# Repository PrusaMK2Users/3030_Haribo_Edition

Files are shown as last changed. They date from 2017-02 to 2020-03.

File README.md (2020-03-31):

# 3030 Haribo Edition



[teaser]: http://i.imgur.com/pz1YWP5.jpg "3030 Haribo Edition in Black"

credit: @arobe

## Unaffiliated Statement

We are **not** affiliated with Prusa Research and the work hereafter was done independently / derived from open source files

We are **not** affiliated with any Facebook group, any one claiming the haribo mod / haribo3030 / zaribo mod / etc is doing so on their own and it's not part of the effort

The **ONLY** official source is this github and the **ONLY** official channel to reach us is listed below (mattermost).  

## Contact us

Please join our [Mattermost](http://3dprinting.community) if you want to reach us.

There is a lot of different topics / channels on there, we welcome all with open arms.

## Disclaimer

**you do this modification at your own risk**

we are not responsible for any damages / injuries that might arise from the usage of all material, including but not limited to ideas, documentation, diagrams, that you get from this github.  All precautions and safety protection should be taken and only attempt it if you are experienced in this area.

## Introduction
Inspiration for the project came from [davtr](http://www.thingiverse.com/davtr/about) mk2 conversion [Prusa i3 MK2-X](http://www.thingiverse.com/thing:1692666)

The use of 3030 extrusion makes the frame very rigid and square.  It takes a lot of the guess work out of building the MK2

The name is from the candy that we get when we buy the MK2 kits.  Somebody jokingly said that's a good name and it sort of stuck.

We welcome any contribution to the project, just open a PR (pull request) and we will review and merge changes

## Haribo in the wild

S3D base settings

- 60mm/s 60% other speeds 30% first layer speed
- 80mm/s 50% other speeds 25% first layer speed
- 100mm/s 40% other speeds 20% first layer speed
- 120mm/s 30% other speeds 15% first layer speed

|\#|username|frame/color|Version|60mm/s|80mm/s|>100mm/s|
|-----|-----|-----|-----|-----|-----|-----|
|0|jtktam|Silver/Orange<br/>Silver/Red<br/>Black/Yellow||Yes|Yes|Yes|
|1|geoffreyc|Silver/Orange||Yes|Yes|Yes|
|2|[ar.o.be](http://imgur.com/a/lWbZ5)|Silver/Pineapple||Yes|Yes|Yes|
|3|[joostvwillegen](http://imgur.com/a/RYOfm)|Black/Metallic Gray<br/>Yellow/Carbon||Yes|Yes|Yes|
|4|chinooktx|Silver/Black||Yes|Yes|Yes|
|5|[skuiper](http://imgur.com/a/5j4W8)|Black/Purple+Green||Yes|Yes||
|6|JJ|Black/Violet|||||
|7|satmanager|Silver/Cherry Red||Yes|Yes||
|8|ryanneufeld|Black/Black|||||
|9|tricko|Black/Black+White||Yes|Yes|Yes|
|10|cube||||||
|11|[johnocfii](http://imgur.com/a/TPEzO)|Black/Jade||Yes|||
|12|[jasonh](http://imgur.com/a/vpMrx)|Silver/Transparent||Yes|Yes|Yes|
|13|jonasrh|Black/GITD green|||||
|14|[evad](http://imgur.com/a/PWNlf)|Silver/Silver||Yes|Yes|Yes|
|15|patrik||||||
|16|abjorshammar||||||
|17|stevendpclark||||||
|18|[arb](http://imgur.com/a/QF9FW)|Silver/Lime Green|||||
|19|[philsburry](http://imgur.com/a/lQyBh)|Silver/Translucent Blue|||||
|20|kaiserheld||||||
|21|tcolby|Silver/White|||||
|22|ollietwist|Silver/Orange|||||
|23|Jb3872|Black/Burgundy|||||
|24|unkle_rukus|Black/Neon Green||Yes|Yes|Yes|
|25|carre55|Black/Orange|||||
|26|dark-nico|Silver/Dark Green|||||
|27|olliet|Silver/Patchwork Colors|||||
|28|cova|Black/Translucent Blue|||||
|29|butthurt_beluga|Silver/Orange|||||
|30|jadam|Black/Black|||||
|31|bg|Silver/Patchwork Colors|||||
|32|curt.darius|Silver/Orange|||||
|33|evil4blue|Silver/Blue|||||
|34|nick|?|||||
|35|actibbs|Silver/Translucent Orange|||||
|36|Cappy175|Black/Lime Green|||||
|37|Grooperdude|Black/Dark Pruple|||||
|38|totalitarian||||||
|39|mloidl|Silver/Melon Yellow||Yes|Yes|Yes|
|40|IcicleTrepan|Black/Green|||||
|41|ballzyk0umpa|Black/Orange|||||
|42|[Dino](https://i.imgur.com/nfYLiFp.jpg)|Black/Pink|MK2.5|Yes|Yes|Yes|
|43|skydriver|Silver/Translucent Green||yes|yes|yes|
|44|kstiers|Black/Translucent Sapphire|||||
|45|christherock23|Black/SkyBlue||||
|46|RiskyBirdness|Silver/Red/Black||Yes|Yes|Yes|
|47|SkyDriver|Silver/Green Metallic||N/A|N/A|N/A| 
|48|cdunham1974|Silver/Translucent Magenta||N/A|N/A|N/A| 
|49|psynautic||||||
|50|[devsfan1830](https://imgur.com/gallery/Fj866qR)|Black/Orange|MK2.5||||
|51|[catrielmuller](https://imgur.com/gallery/VBMNfim)|Black/Black|MK2s MMU|Yes|Yes|Yes|

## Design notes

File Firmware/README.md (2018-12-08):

# Firmware

## Releases

Pre-compiled HEX releases can be found here: https://github.com/PrusaMK2Users/Prusa-Firmware/releases

## Introduction

The 3030 Haribo Edition frame has slightly more Z height than the stock Original Prusa i3 MK2. You will need to make some minor modifications to the firmware in order to accommodate for this.

## Warning

**Please Note:** Depending on the y carriage you use (stock or aftermarket), your mileage might vary.  Various y-carriages have different heights. I will note where you need to make the necessary changes and how to determine the values, but be ready to shut down the machine if it looks like it's going to crash the head into the bed!

## Configuration_prusa.h

Let's change the name of the printer:

```
// Printer name
#define CUSTOM_MENDEL_NAME "3030 Haribo Edition"
```

Let's set the correct Z_MAX_POS, the originial value is 210, and after a few test builds we determine 220 works on the MK2 and MK2s

so let's set it to 220:

```
#define Z_MAX_POS 220
```

If using the MK2.5 you'll need to change the Z_MAX_POS to 225mm due to the new MK52 bed

so let's set it to 225:

```
#define Z_MAX_POS 225
```

## Configuration.h

Since we are in here anyways, let's fix the encoder too:

```
#define ENCODER_PULSES_PER_STEP 2 // Increase if you have a high resolution encoder
#define ENCODER_STEPS_PER_MENU_ITEM 2 // Set according to ENCODER_PULSES_PER_STEP or your liking
```

to

```
#define ENCODER_PULSES_PER_STEP 4 // Increase if you have a high resolution encoder
#define ENCODER_STEPS_PER_MENU_ITEM 1 // Set according to ENCODER_PULSES_PER_STEP or your liking
```

## pins.h (optional)

Now depending which LCD board you have, you might find the rotary wheel direction is not intuitive (goes up when you expect down, down when up).  It's fairly easy to fix.  You need to invert 2 numbers in pins.h  

Find the first occurence of the following lines:
```
#define BTN_EN1 72
#define BTN_EN2 14
```

These are the atmega pin numbers assigned to the up and down motion of the menus.  To invert them, simply swap the numbers so the lines become:
```
#define BTN_EN1 14
#define BTN_EN2 72
```

## Final step

Now compile and upload the firmware.. redo your xyz calibration as normal

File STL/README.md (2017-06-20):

# STL

## Quantity to print
Beginning of each filename denotes the quantity of that part you need to print.

for example

1x_power_supply_box.stl means you should print one.

## Stock MK2 parts

Any parts not found in this github you can find on [prusa research github](https://github.com/prusa3d/Original-Prusa-i3/tree/MK2)

## Print settings

All models should be printed as oriented in the STL files

No supports are needed

30% infill, triangular or fast honeycomb for strength
3/3/2 top/bottom/perimeters
0.2mm layer height
PETG is preferred

ABS might have shrinkage issues on some parts
PLA is not preferred, will eventually need replacements due to fatigue

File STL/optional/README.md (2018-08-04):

# Optional STL

_These files are optional stuff to print for the Haribo Edition_

|Filename|Author|Description|
|-----|-----|-----|
|1x 67.75mm Jig.stl|jtktam|A jig to set the spacing of the left y rod holders to 67.75mm.  don't worry if it's not dead on, the idea is using this will ensure the front and back *LEFT* side y rod holders are the same distance from the left edge of the extrusion.  the holes are for M6 x 12 bolts and t-nuts, it's *suppose* to be loose so you can slide it in and out quickly.  Tested and it works to ensure the left side is good to go|
|1x_aftermarket_y_carriage_raiser.stl|jtktam (Joseph Tam)|three sc8uu block spacers and 1 belt holder spacer to raise the y carriage by 3.5mm to match the level of the stock y carriage|
|1x_fan-nozzle-haribo.scad<br/>1x_fan-nozzle-haribo.stl|jonasrh (Jonas Hansen)|a special version of the fan nozzle with "Haribo" on it|
|1x_lcd_cover.stl<br/>1x_lcd_cover.scad<br/>BPreplayBold.otf|Cova (Rob Baumstark)|Updated version of the LCD cover with '3030 Haribo Edition'. SCAD source included to generate custom LCD covers with your number in the corner and optionally updated text for dual-color.<br/>Included BPreplay font required to compile the SCAD source.|
|1x_lcd_cover_text.stl|Cova (Rob Baumstark)|STL of the text in the LCD cover for dual-color prints.|
|1x_lcd_mount_3030_clips.stl|nrepian|Modified LCD mount to use clips, rather than insert|
|1x_lcd_mount_3030_extra_contrast_clearance.stl|nrepian|3030 LCD clips with additional clearance for contrast pot|
|1x_lcd_mount_extra_contrast_clearance.stl|stevendpclark (Steven Clark)|A version of the LCD mounts that provide more clearance for the contrast pot for 3rd Party 2004 LCD Smart Controller Display boards.|
|1x_mk2x_y_belt_holder.stl|Mk2-x|demoted y belt holder|
|1x_mk2x_y_belt_holder_modded.stl|chinooktx (Pat Brochu)|modded y belt holder from mk2x (added 2mm)|
|1x_power_supply_box.stl<br/>1x_power_supply_mount.stl|jtktam (Joseph Tam)|Power supply mount and switch box for ebay PSU|
|1x_rambo_mount.stl|ryanneufeld (Ryan Neufeld)|Adapter plate to allow using the Prusa rambo enclosure.|
|1x_z_motor_mounts_three_screw.stl|dino (Garrett B)|Removed front inner screw holes to prevent collisions with pinda/fan nozzle|
|3x_double_y_bearing_housing.stl|Mk2-x|demoted y bearing holder|
|3x_SC8UU_LM8UU.stl|jtktam (Joseph Tam)|adapt lm8u to sc8uu block, use for aftermarket y carriage|
|3x_SC8UU_RZJM.stl|jtktam (Joseph Tam)|adapt igus rjzm to sc8uu block, use for aftermarket y carriage|
|3x_y_bearing_housing_lm8uu_short.stl|chinooktx (Pat Brochu)|adapt lm8uu to y belt bearing|
|3x_y_bearing_housing_rjzm_01_08.stl|chinooktx (Pat Brochu)|adapt igus rjzm to y belt bearing|
|7x_tsun_end_cap.stl|Cova (Rob Baumstark)|End caps designed to fit T-Sun 3030 extrusion|
|16mm Tnut Spacing|davvyk/dino (Garrett B)|Widened spacing between blocks to accomodate 15.8mm Tnuts|
|i3 Haribo Rambo Mount Thin.stl|ARBBB|Use for mounting standard rambo enclosure to the Haribo extrusions.|
|LED_Holder_Haribo_v3.stl | John O'Shaughnessy (johnocfii) and Patrik Rosén (patrik) | LED Strip/Bar Holders that attach to the back side of the Haribo frame.  Use this if you didn't use plastic L brackets on the top of the Z frame or if you did use plastic L brackets but only need a narrow area to hold your LEDs as the L brackets will prevent you from using the full back side of the extrusion.|
|LED_Holder_Haribo_v3_Bracket_Mount.stl | IcicleTrepan | Yet another alternate version of the excellent LED Strip/Bar Holder by John/Patrik.  This one can attach to the back side of the extrusion over top of the L brackets, giving you use of most of the back side of the Z frame's extrusion (still have to watch out for the hex screws).  NOTE:  It may be easier to install beside the bracket and then slide over the bracket than to install directly on the bracket.|
|LED_Holder_Haribo_v3_Reversed_Mount.stl | IcicleTrepan | Alternate version of the excellent LED Strip/Bar Holder by John/Patrik.  This one attaches to the front side of the Haribo frame.  Use this if you did use plastic L brackets on the Z frame and would like the holders spread out further.|
|LRS-350-12-bottom.stl|chinooktx (Pat Brochu)|Initial design for LRS-350-12 Meanwell Power Supply bottom cover|
|LRS-350-12-top.stl|chinooktx (Pat Brochu)|Initial design for LRS-350-12 Meanwell Power Supply top bracket|
|LRS-350-Neuf/LRS-350 Enclosure (lid and body) | Ryan Neufeld | Enclosure designed for IEC with integrated switch, and a removable lid for ease of access. Use M3x8mm fasteners w/ M3 nuts. Optionally you can use M3x10 or longer if you don't want to use nuts the hole beyond the nut is sized for direct threading of M3 fasteners.| 
|MK2S-modified-y-belt-holder.stl| Ryan Neufeld | A wider version of the stock mk2s belt holder, allows for re-positioning to better align with the PINDA when homing.|
|MK2S-modified-y-belt-holder-3mm-taller.stl| Ryan Neufeld | As above, only pushes the belt down 3mm, this is to be used in leiu of the belt holder spacer when using the half height bed frame.|
|Spool-holder-slide-top.stl|MoshiBin | A spool holder that sits on top of the frame, slides from the side of the top extrusion. Modeled to be similar to the "B4" MK3 spool mount.|

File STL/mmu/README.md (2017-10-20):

# Multi-Material Upgrade Parts

|Filename|Author|Description|
|-----|-----|-----|
|1x_e_motor_holder.stl| Ryan Neufeld (ryanneufeld)  | Remixed mounts for the mmu extruders. You need one per pair of colors. 2 colors == one part, 4 colors == two parts | 
|1x_superswitch_adapter.stl | Ryan Neufeld (ryanneufeld) | An adapter plate that will allow you to use the Prusa superswitch enclosure on the haribo. |
|1x_superswitch_mount.stl | RydinX (Jonas Hansen) | A superswitch mount inspired by the rambo mount designed by Joseph Tam|

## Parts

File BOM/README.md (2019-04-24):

# I. Introduction
Below you will find the Bill of Materials for the **3030 Haribo Edition** build. This BOM will help you to either **upgrade** your **Original Prusa i3 MK2** or **scratch-build** a printer. Each section contains a subheading to indicate if it's required for an **upgrade** or just a **scratch-build**. If you have questions about this build, feel free to submit a Github issue and we will be glad to help you.

# II. Aluminum Frame Parts / Smooth Rods / Rubber Feet
#### Required For: **Upgrade** / **Scratch-Build**
This section contains the frame parts, smooth rods, t-slot nuts, and rubber feet that you will need.

If you live in the United States, the recommended seller of these parts is [Misumi US](https://us.misumi-ec.com/). To simplify the ordering process from Misumi, we have created a [Misumi CSV guide here](./MISUMI_CSV/README.md). You can simply download a pre-made data file and upload it to your cart to order all of the required parts.

If you would rather source the frame parts elsewhere, below is a list of all of the frame parts you will need.

#### Parts List

|Qty|Misumi Part #|Description|
|-----|-----|-----|
|3|HFS6-3030-354-Z8-XA12-XB342|Clear anodize 3030 Normal Rigidity Type extrusion 354mm 8mm counterbore hole @ 12mm and 342mm (x)|
|2|HFS6-3030-320-TPW-Z8-XA100|Clear anodize 3030 Normal Rigidity Type extrusion 320mm tap both ends 8mm counterbore hole @100mm (y)|
|2|HFS6-3030-330-TPW|Clear anodize 3030 Normal Rigidity Type 330mm tap both ends (z)|
|2|PSFG8-370|Hard Chrome Precision Linear Shaft - Straight 370mm (x)|
|2|PSFG8-360|Hard Chrome Precision Linear Shaft - Straight 360mm (y)|
|2|PSFG8-320|Hard Chrome Precision Linear Shaft - Straight 320mm (z)|
|1|PACK-HNTTSN6-6|Pre-Assembly Insertion Short Nuts -For HFS6 Series Aluminum Extrusions (100 per pack)|
|4|C-30-RK-3617|Rubber Feet|

#### Misc Misumi Parts (Scratch build only)

|Qty|Misumi Part #|Description|
|-----|-----|-----|
|2|WM5-15|Extruder Springs (5x15mm)|
|1|PSFR5-16|Extruder idler bearing rod(5x16mm)|

#### Spool Holder Parts List (OPTIONAL)
If you would like to build an integrated spool holder, there are a few other parts you will need.

|Qty|Misumi Part #|Description|
|-----|-----|-----|
|1|HFS6-3030-200-Z8-XA15|Clear anodize 3030 High Rigidity Type extrusion 200mm 8mm counterbore hole @ 15mm (spool holder vertical)|
|1|HFS6-3030-147-LTP|Clear anodize 3030 High Rigidity Type extrusion 147mm tap left end (spool holder horizontal)|
|1|SHBLBSL6|Brackets - 6 Series, Blind Brackets |

# III. Mounting Hardware
#### Required For: **Upgrade** / **Scratch-Build**

You will need some various nuts and bolts in order to assemble your **3030 Haribo Edition**. Below you will find a list of required hardware for both an upgrade build and a scratch printer build.

#### Recommended sources for this section (United States)
- [Bolt Depot](http://www.boltdepot.com/)
- [McMaster-Carr](https://www.mcmaster.com)
- [Fastenal](https://www.fastenal.com/)

#### Parts List
|Qty|Description|
|-----|-----|
|36|M6 washer|
|9|Socket Head Cap Screw M8 x 40mm|
|12|Socket Head Cap Screw M6 x 12mm|
|54|Socket Head Cap Screw M6 x 14mm|
|4|Socket Head Cap Screw M6 x 20mm|

# IV. Bushings
If you are upgrading from an Original Prusa i3 MK2, you may re-use the **LM8UU** bushings for X, Y and Z axes. However, you may consider swapping the X and Y axes with IGUS Drylin® Bushings. **Caution**: It is NOT recommended to use these bushings on the Z axis, as it is prone to binding on the **3030 Haribo Edition**.

#### Parts List
|Qty|Part #|Description|
|-----|-----|-----|
|6|RJ4JP-01-08|IGUS DRYLIN® Bushing|

#### Recommended sources for this section (United States)
- [Folger Technologies](https://goo.gl/oc9qrd)

# V. Scratch Build Parts
#### Required For: **Scratch-Build**
This section is only required for users who are building a **3030 Haribo Edition** from scratch.

#### Parts List

|Qty|Part #|Source|Description|
|-----|-----|-----|-----|
|1|PRI-UPG-MK2-ORG|[Prusa Research](https://goo.gl/39exUd)|Original Prusa i3 Plus to MK2 upgrade kit |
|1|-|[ultimachine](https://goo.gl/L4XLX0)|Rambo Mini v1.3 |
|1|LRS-350-12|[Arrow](https://goo.gl/zRQ6IZ) |Meanwell LRS-350-12 12V 29A 348W Power Supply |
|1|-|eBay / aliexpress|IEC power socket |
|1|-|eBay / aliexpress|Power switch |
|1|E-FAN-50-50-15|[e3D](https://goo.gl/qESKpZ)|50x50x15mm 12v DC Side Blow Fan |
|1|-|[RepRap Champion](https://goo.gl/xK2OkY) / eBay / aliexpress| Smart controller Reprap 2004 LCD |
|2|-|eBay / aliexpress|2x5 ribbon cable (>40cm) |
|-|-|Electronics Store|14awg power wire (black/red) |
|-|-|Electronics store|14awg ferrules |
|-|-|Electronics Store|Short zip ties (just get a bag full) |
|1|-|Electronics Store / Amazon | Wire loom (3/8" or 10mm) (For wire management)|
|1|-|[RepRap Champion](https://goo.gl/54I3IC) / eBay / aliexpress|Prusa i3 Universal Y Carriage Plate|
|2|-|[RepRap Champion](https://goo.gl/VUj4mo) / eBay / aliexpress|GT2 16T pulley|
|4|F623ZZ|eBay / aliexpress|F623ZZ 3x10x4mm flanged bearing. Put two of them together so the flange size faces out as belt idler. |
|1|104138|eBay / Hobby Store|HPI Blitz / Firestorm Titanium Idler Gear Shaft 5x16m #104138 (For extruder idler bearing rod)|
|4|-|[RepRap Champion](https://goo.gl/8F2Ub6) / eBay / aliexpress|LM8UU linear bearing (Bearings for the X Ends (Z Movement Direction) |
|8|-|McMaster / Fastenal / Bolt Depot | M3 fender washer |
|2|-|McMaster / Fastenal / Bolt Depot | M5 fender washer |
|4|-|McMaster / Fastenal / Bolt Depot | M2 washer |
|14|-|McMaster / Fastenal / Bolt Depot | M3 washer |
|6|-|McMaster / Fastenal / Bolt Depot | M3 square nut |
|2|-|McMaster / Fastenal / Bolt Depot | M3 lock nut|
|9|-|McMaster / Fastenal / Bolt Depot | M3 hex nut|
|4|-|McMaster / Fastenal / Bolt Depot | Socket Head Cap Screw M2 x 12mm|
|15|-|McMaster / Fastenal / Bolt Depot | Socket Head Cap Screw M3 x 10mm|
|6|-|McMaster / Fastenal / Bolt Depot | Socket Head Cap Screw M3 x 12mm|
|10|-|McMaster / Fastenal / Bolt Depot | Socket Head Cap Screw M3 x 18mm|
|3|-|McMaster / Fastenal / Bolt Depot |Socket Head Cap Screw M3 x 20mm|
|2|-|McMaster / Fastenal / Bolt Depot |Socket Head Cap Screw M3 x 25mm|
|3|-|McMaster / Fastenal / Bolt Depot |Socket Head Cap Screw M3 x 30mm|
|3|-|McMaster / Fastenal / Bolt Depot |Socket Head Cap Screw M3 x 40mm|
|5|-|McMaster / Fastenal / Bolt Depot |Button Head Cap Screw M3 x 8mm|
|4|-|McMaster / Fastenal / Bolt Depot |Button Head Cap Screw M3 x 10mm|
|2|-|McMaster / Fastenal / Bolt Depot |Button Head Cap Screw M3 x 12mm|
|4|-|McMaster / Fastenal / Bolt Depot |Button Head Cap Screw M4 x 6mm|
|9|-|McMaster / Fastenal / Bolt Depot |Socket Head Cap Screw M8 x 40mm|
|12|-|McMaster / Fastenal / Bolt Depot |Socket Head Cap Screw M6 x 12mm|
|54|-|McMaster / Fastenal / Bolt Depot |Socket Head Cap Screw M6 x 14mm|
|4|-|McMaster / Fastenal / Bolt Depot |Socket Head Cap Screw M6 x 20mm|

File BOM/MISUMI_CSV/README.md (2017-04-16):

# Introduction
Regardless of whether you are upgrading from an existing Original Prusa i3 MK2,
or building a 3030 Haribo Edition from scratch, you will need to order aluminum
extrusions, smooth rods, t-slot nuts. Our current recommended source for these
parts (for those living in the US) is from [Misumi USA](https://www.misumi-ec.com/us).

To make the Misumi ordering process simpler, we have put together a CSV (Comma-separated Value) file containing all of the parts for the 3030 Haribo Edition. This file can be uploaded to your Misumi cart using the instructinos below.

# 1. Pick your color!
Decide whether you would like a silver frame or a black frame. Choose a color and then download the appropriate corresponding CSV file below based on your selection.

- [Silver 3030 Frame CSV File](./Misumi_Haribo_Upgrade_Parts_Silver.csv)
- [Black 3030 Frame CSV File](./Misumi_Haribo_Upgrade_Parts_Black.csv)

# 2. Do you also want an integrated spool holder?
If you would like to also build a spool holder, you can also download a CSV file containing those additional parts below:

- [Silver](./Misumi_Haribo_SpoolHolder_Silver.csv)
- [Black](./Misumi_Haribo_SpoolHolder_Black.csv)

# 3. Order the parts!

- **Step 1.** Register an account with Misumi [here](https://us.misumi-ec.com/contents/regist/)
- **Step 2.** Login to your Misumi account.
- **Step 3.** Select the "Order" link at the top of the page.

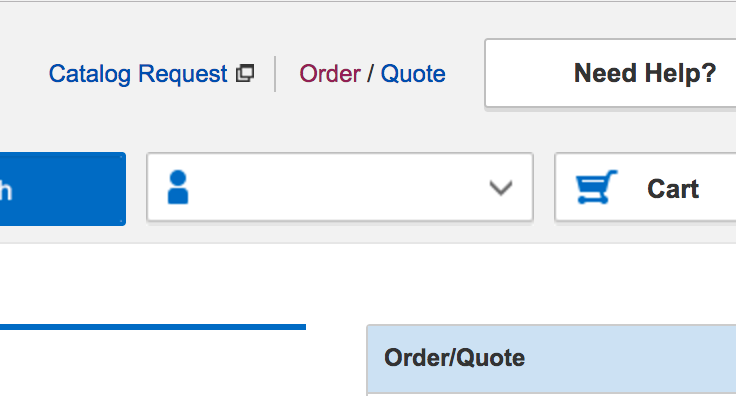
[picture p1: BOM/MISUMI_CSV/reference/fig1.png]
Order Link


- **Step 4.** Scroll down to the bottom of the "Create Order Request" page and click "Import from File".

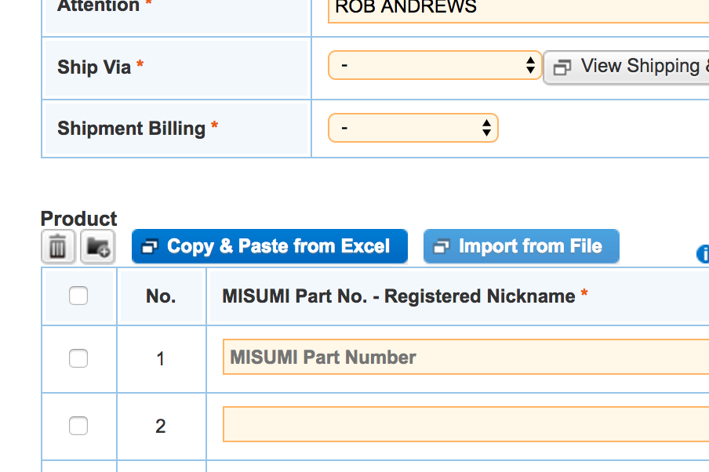
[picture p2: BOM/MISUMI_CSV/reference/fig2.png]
Import From File


- **Step 5**. On the "Import From File", select "Choose File" and select the CSV for the main Haribo parts that you previously downloaded. This file should begin in "Misumi_Haribo_Upgrade_Parts_". If you also downloaded the spool holder CSV, repeat this process once you have finished importing the first CSV file by returning to Step 4.

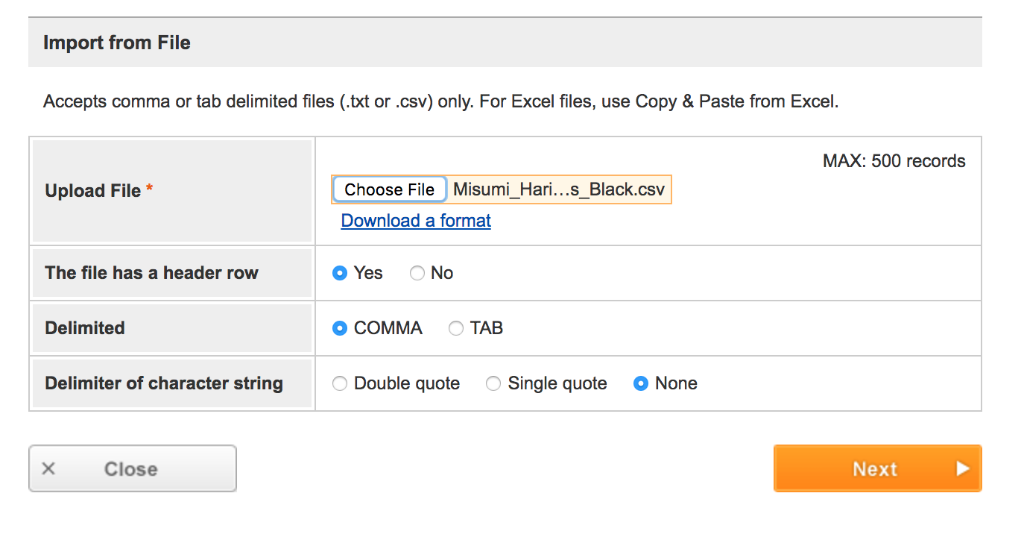
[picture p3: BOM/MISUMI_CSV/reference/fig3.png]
Import CSV


- **Step 6.** On the "Import From File" screen, verify you select the following options:
  - **This file has a header row**: `Yes`
  - **Delimited**: `COMMA`
  - **Delimiter of character string**: `None`
- **Step 7.** Click 'Next' on the "Import from File" screen.
- **Step 8.** Click 'Next' on the "Set Item" screen.

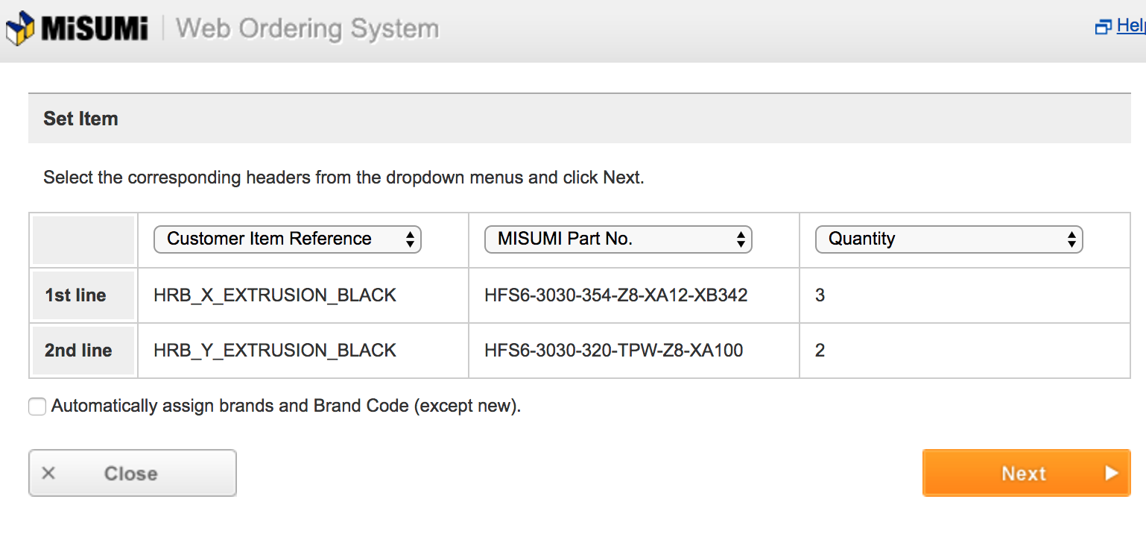
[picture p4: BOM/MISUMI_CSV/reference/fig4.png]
Set Item Screen


- **Step 9.** The items should now be in your cart.
- **Step 10.** If you would like to upload the CSV for the Optional Spool Holder, continue back to **Step 4**. Otherwise, continue to **Step 11**.
- **Step 11.** Continue to fill out the remainder of the Order Form and submit your Misumi order. Congrats on ordering your Haribo parts!

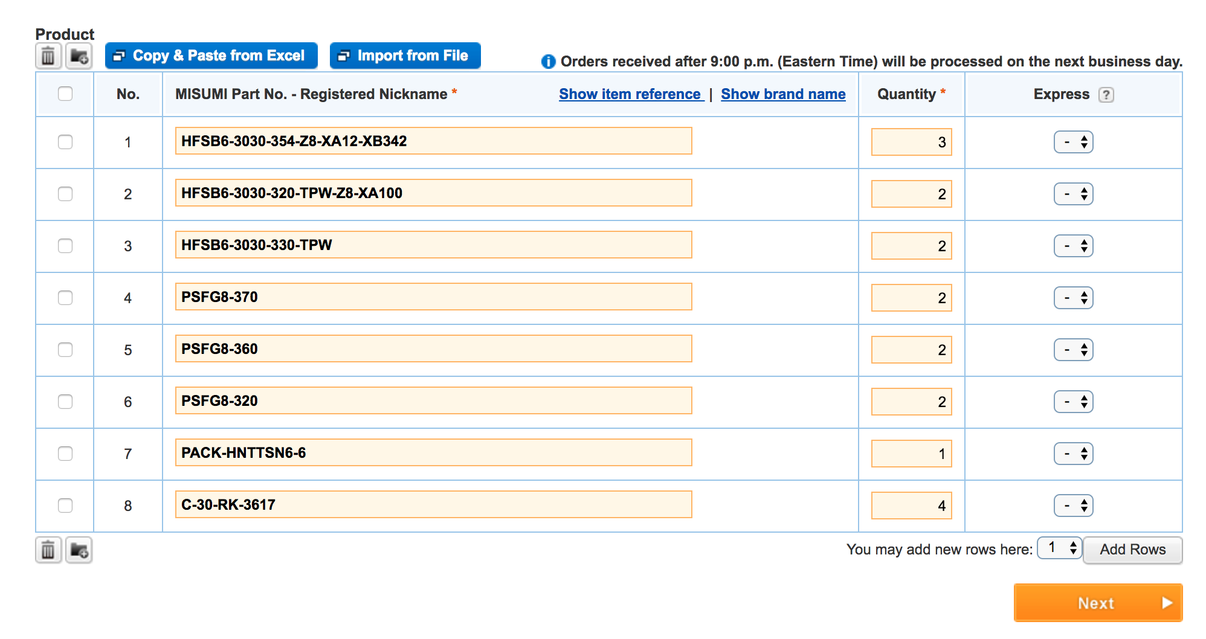
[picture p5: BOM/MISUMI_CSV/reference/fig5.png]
Items Added to Cart


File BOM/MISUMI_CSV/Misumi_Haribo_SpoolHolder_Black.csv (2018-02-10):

Customer Item Reference | MISUMI Part No. - Registered Nickname | Quantity
HRB_SPOOLHOLDER_HORZ_BLACK | HFSB6-3030-200-Z8-XA15 | 1
HRB_SPOOLHOLDER_VERT_BLACK | HFSB6-3030-147-LTP | 1
HRB_MOUNTING_BRACKET | SHBLBSL6 | 1

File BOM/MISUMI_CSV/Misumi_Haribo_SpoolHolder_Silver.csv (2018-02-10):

Customer Item Reference | MISUMI Part No. - Registered Nickname | Quantity
HRB_SPOOLHOLDER_HORZ_SILVER | HFS6-3030-200-Z8-XA15 | 1
HRB_SPOOLHOLDER_VERT_SILVER | HFS6-3030-147-LTP | 1
HRB_MOUNTING_BRACKET | SHBLBSL6 | 1

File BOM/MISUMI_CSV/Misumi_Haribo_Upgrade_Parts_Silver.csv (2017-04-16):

Customer Item Reference | MISUMI Part No. - Registered Nickname | Quantity
HRB_X_EXTRUSION_SILVER | HFS6-3030-354-Z8-XA12-XB342 | 3
HRB_Y_EXTRUSION_SILVER | HFS6-3030-320-TPW-Z8-XA100 | 2
HRB_Z_EXTRUSION_SILVER | HFS6-3030-330-TPW | 2
HRB_X_SMOOTH_ROD | PSFG8-370 | 2
HRB_Y_SMOOTH_ROD | PSFG8-360 | 2
HRB_Z_SMOOTH_ROD | PSFG8-320 | 2
HRB_T_SLOT_NUTS | PACK-HNTTSN6-6 | 1
HRB_RUBBER_FEET | C-30-RK-3617 | 4

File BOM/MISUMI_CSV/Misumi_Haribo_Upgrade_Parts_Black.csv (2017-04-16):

Customer Item Reference | MISUMI Part No. - Registered Nickname | Quantity
HRB_X_EXTRUSION_BLACK | HFSB6-3030-354-Z8-XA12-XB342 | 3
HRB_Y_EXTRUSION_BLACK | HFSB6-3030-320-TPW-Z8-XA100 | 2
HRB_Z_EXTRUSION_BLACK | HFSB6-3030-330-TPW | 2
HRB_X_SMOOTH_ROD | PSFG8-370 | 2
HRB_Y_SMOOTH_ROD | PSFG8-360 | 2
HRB_Z_SMOOTH_ROD | PSFG8-320 | 2
HRB_T_SLOT_NUTS | PACK-HNTTSN6-6 | 1
HRB_RUBBER_FEET | C-30-RK-3617 | 4

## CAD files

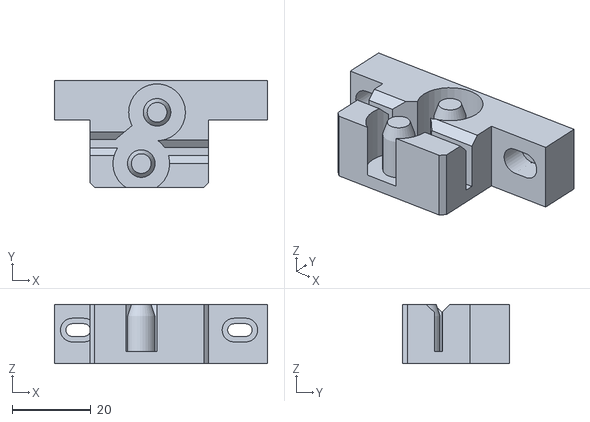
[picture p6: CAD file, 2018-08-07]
STL/1x_y_belt_holder.stl
54.0 x 27.0 x 15.0

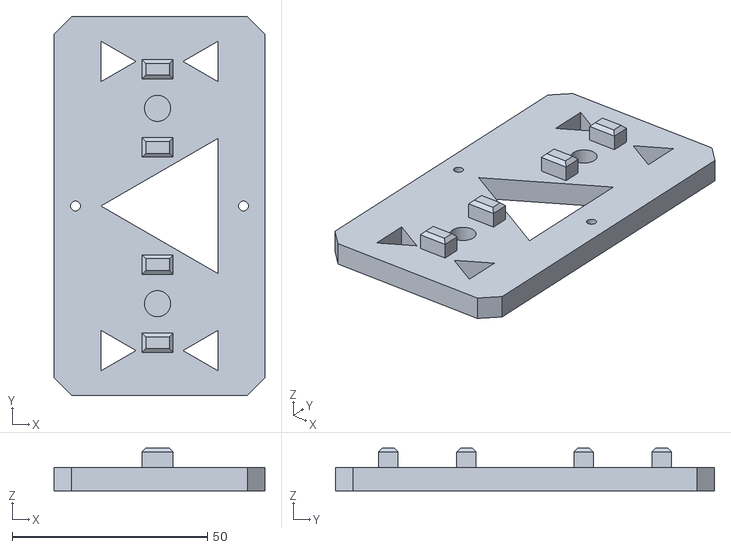
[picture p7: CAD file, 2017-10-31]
STL/mmu/1x_superswitch_v2_mount.stl
54.0 x 97.0 x 11.0

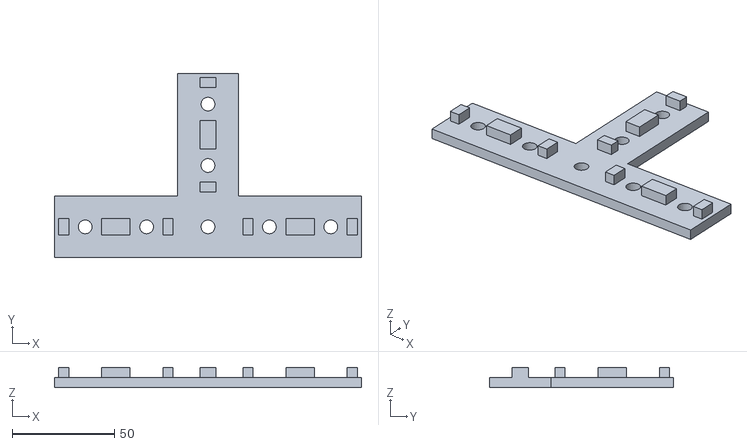
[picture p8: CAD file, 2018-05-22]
STL/optional/16mm Tnut Spacing/2x_T_bracket_16mm.stl
150.0 x 90.0 x 10.0

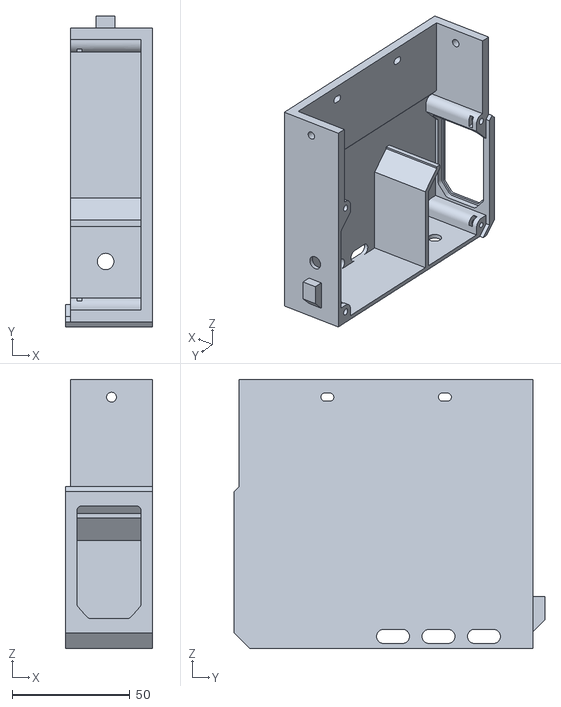
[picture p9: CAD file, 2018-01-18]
STL/optional/LRS-350-Neuf/1x_LRS-350_enclosure_body.stl
37.1 x 132.1 x 114.4

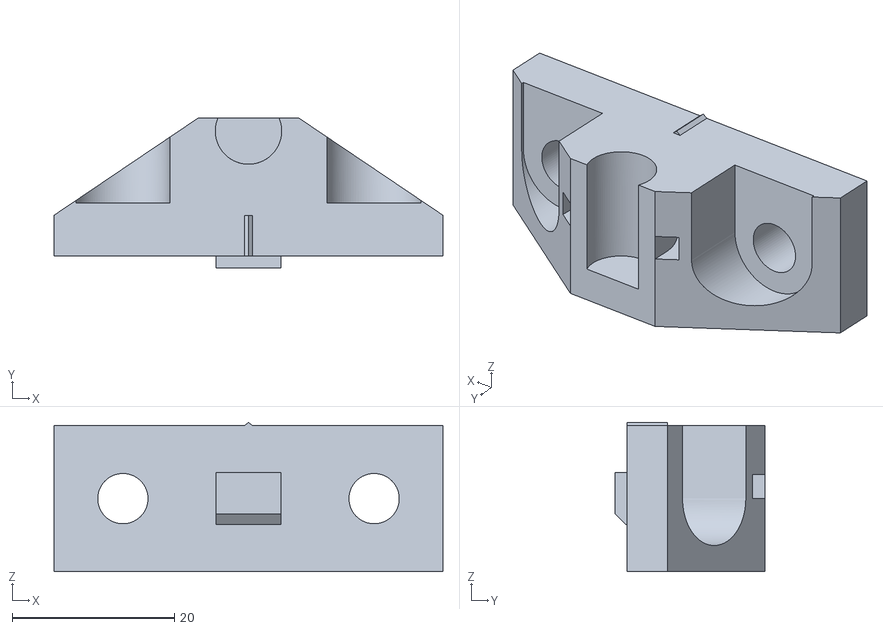
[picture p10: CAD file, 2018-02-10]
STL/square_slot_extrusions/4x_y_rod_holder_SSE.stl
48.0 x 18.5 x 18.4

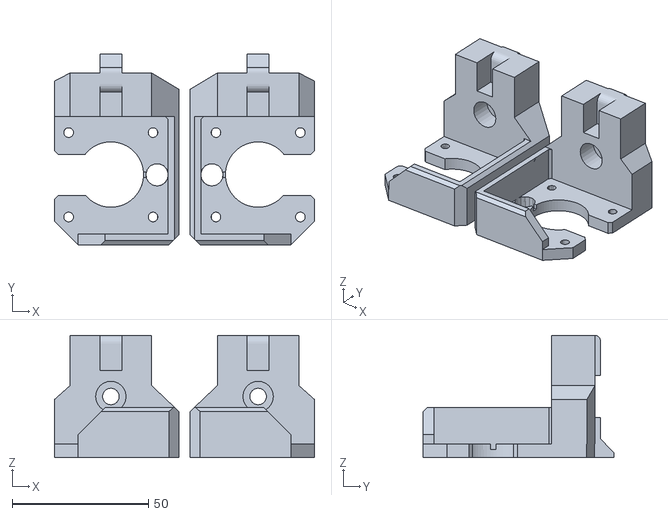
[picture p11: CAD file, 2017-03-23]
STL/1x_z_motor_mounts.stl
95.5 x 70.0 x 45.0

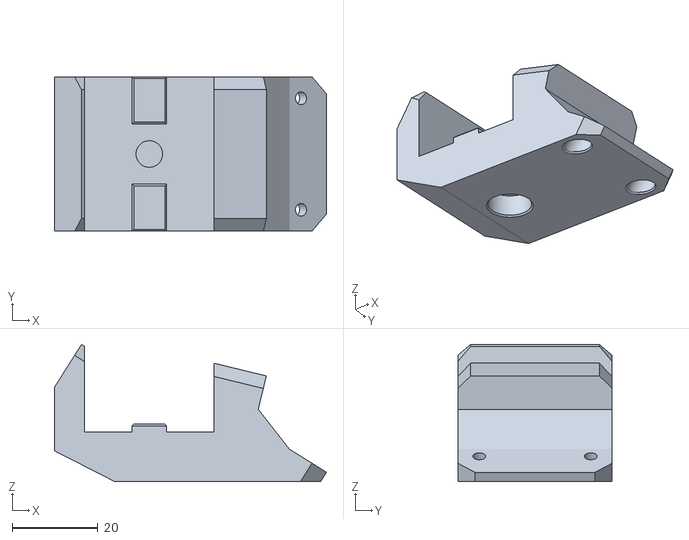
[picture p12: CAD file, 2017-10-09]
STL/mmu/1x_e_motor_holder.stl
63.4 x 36.0 x 31.9

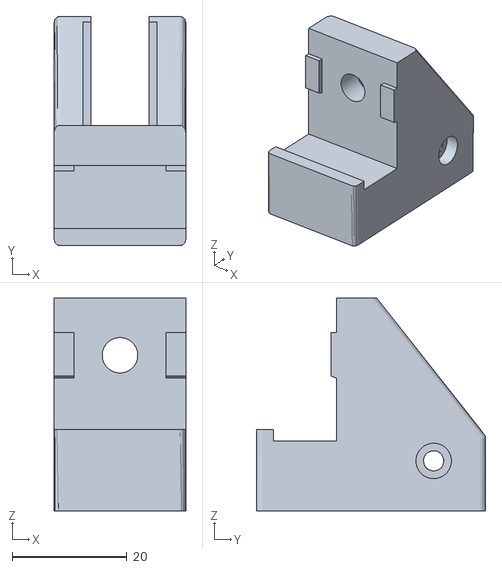
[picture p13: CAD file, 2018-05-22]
STL/optional/16mm Tnut Spacing/1x_y_idler_16mm.stl
23.0 x 40.0 x 37.2

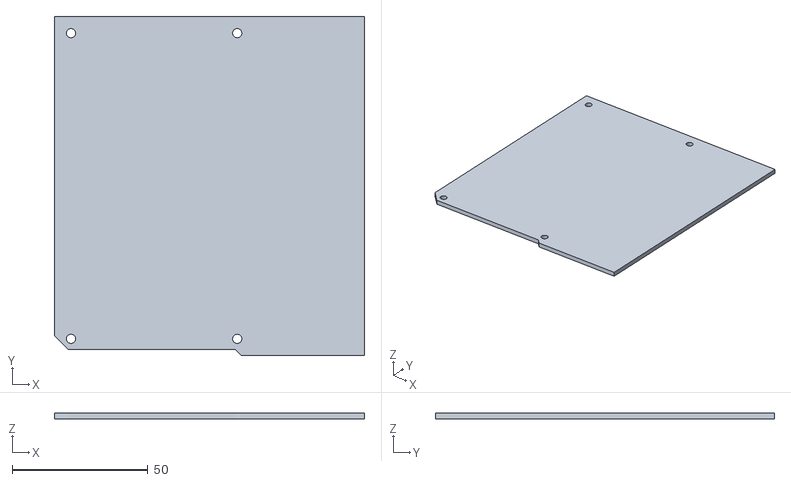
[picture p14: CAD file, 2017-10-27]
STL/optional/LRS-350-Neuf/1x_LRS-350_enclosure_lid.stl
114.4 x 125.0 x 2.15

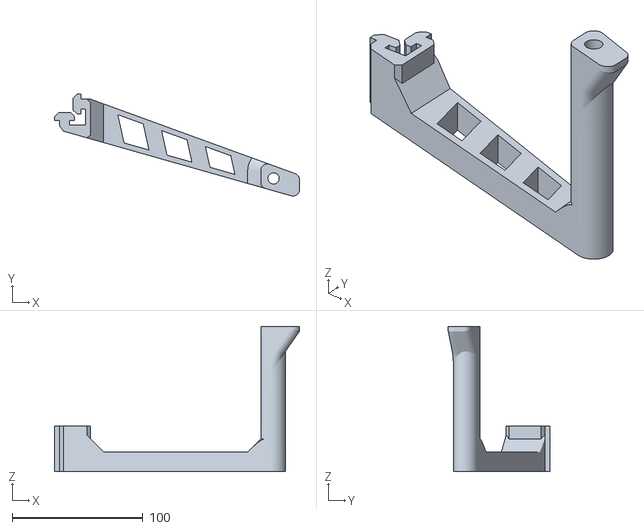
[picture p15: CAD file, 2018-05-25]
STL/optional/Spool-holder-slide-top.stl
187.4 x 78.1 x 111.0

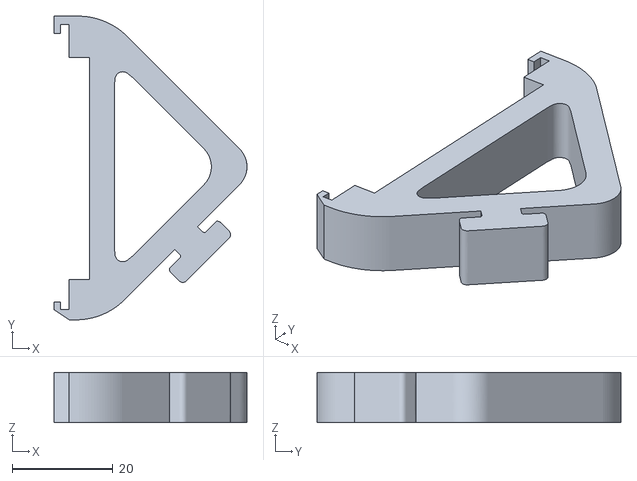
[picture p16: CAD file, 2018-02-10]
STL/square_slot_extrusions/1x_lcd_mount_extended_pcb_ears_part1_SSE.stl
38.3 x 60.2 x 10.0

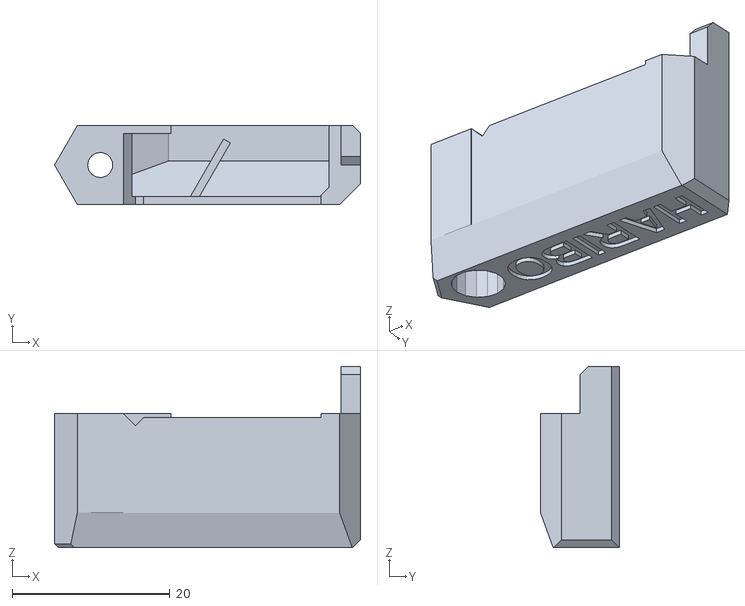
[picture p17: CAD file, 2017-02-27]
STL/1x_fan-nozzle-haribo.stl
38.8 x 10.0 x 23.0

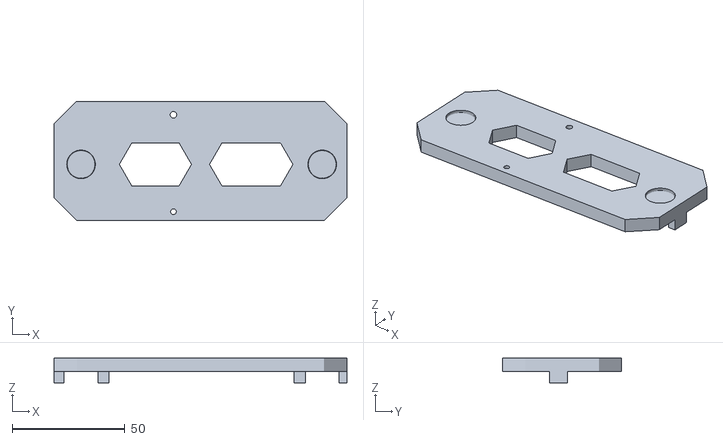
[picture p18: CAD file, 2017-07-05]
STL/mmu/1x_superswitch_adapter.stl
130.0 x 53.0 x 11.0

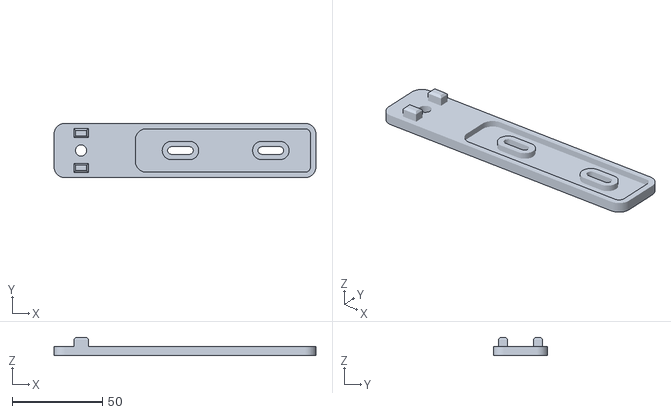
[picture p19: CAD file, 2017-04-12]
STL/optional/LRS-350-Neuf/1x_LRS-350_psu_upper_strap.stl
145.0 x 30.0 x 10.0

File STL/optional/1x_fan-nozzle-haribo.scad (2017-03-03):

module fan_nozzle(){
    difference(){    
        union(){
            cube([32,10,17]); // Main cube
            translate([30,5,0])cylinder(r=5.8,h = 17, $fn=6);    
            translate([-3,0,-6]) cube([3,10,23]);
            //#translate([-2,5,0])cylinder(r=5.8,h = 17, $fn=6);        
        }

        // Mounting screw
        translate([30,5,-10])cylinder(r=3.2/2,h = 24.5-0.2, $fn=15); // Screw cut
        translate([30,5,17-3.5])cylinder(r=3.1,h = 20, $fn=15); // head cut

        //#translate([-2,5,-10])cylinder(r=3.2/2,h = 24.5-0.2, $fn=15); // Screw cut
        //#translate([-2,5,17-3.5])cylinder(r=3.1,h = 20, $fn=15); // head cut

        // Fan entry hole
        translate([1,10-1.5,-1])cube([20,3,16.5]);
        translate([1,10-1.5,-1-5])cube([18,3,16.5]);
    
        // Airway cutout
        difference(){    
            translate([1,1,-1])cube([25,8,16.5]);    
            translate([0,0,10])rotate([45,0,0])cube([30,8,16.5]);    
            translate([-1,-10,-1])rotate([0,0,45])cube([10,8,30]); 
            translate([20,0,16])rotate([0,20,0])cube([10,20,10]);    
        }
        translate([2,-1,-4.5])cube([24,3,5]);
        //#translate([-2,-1,-2])rotate([0,45,0])cube([5,10,5]);
        translate([22,-1,-2])rotate([0,45,0])cube([5,10,5]);
    }

    // Air director
    translate([18,0,7])rotate([0,0,30])cube([1,9,10]);
}

module fancy_corners(){
    translate([-10,-10.5,13])rotate([-20,0,0])cube([50,10,15]);
    translate([-16,-10.5,17.5])rotate([0,45,0])cube([10,30,15]);
    
    translate([46.5,-10.5,15])rotate([0,-45,30])cube([10,30,15]);
    translate([28.62,-10.5,15])rotate([0,-45,-30])cube([10,30,15]);

    translate([-5,-1,-7])rotate([0,0,0]) cube([10,6,7]);
    translate([-0.5,-1,-7])rotate([0,0,0]) cube([1,15,7]);
    translate([-5,4,-11])rotate([45,0,0]) cube([10,5,5]);

    //left cut
    translate([-6.5,-8,-5])rotate([0,0,45])cube([10,10,45]);
    translate([-7,-5,12])rotate([0,-45,0])cube([10,30,15]);
    
    translate([-7,5,-10])rotate([0,0,45])cube([10,10,35]);
}

module fan_n(){
    difference(){
        fan_nozzle();
        fancy_corners();    
        translate([-1,3.5,16.5])linear_extrude(height = 0.6){
            text("HARIBO", size = 5, font = "Helvetica Neue:style=Bold");
        }
    }
}

module printable_fan_n() {
    rotate([0,180,0]){
        fan_n();
    }
}

printable_fan_n();

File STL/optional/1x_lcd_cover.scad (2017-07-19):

// PRUSA iteration3
// LCD cover
// GNU GPL v3
// Josef Průša <iam@josefprusa.cz> and contributors
// http://www.reprap.org/wiki/Prusa_Mendel
// http://prusamendel.org


// Modified by Rob Baumstark <rbaumstark@gmail.com>
// for the 3030-Haribo Project
// https://github.com/PrusaMK2Users/3030_Haribo_Edition

// BPreplay font included is licensed under the SIL Open Font License.
// http://scripts.sil.org/OFL

// Instructions:

// If you want a number in the top-left corner, change the haribo_number value below to your number. If haribo_number is set to 0 then the corner is left blank.

// By default the text is engraved into the cover - if you need a second STL of the text to do a dual-color print, after exporting the cover to an STL, comment out the lcd_cover(); line below (put two /'s in front of it), and uncomment the colortext(); line, then compile and export again.

// --------------------------------------------------
// End-user configuration section - edit as required.
haribo_number = 0;
lcd_cover();
//colortext();
// --------------------------------------------------
// Do not edit below this point.

use <BPreplayBold.otf>


module main_body(){
difference() {
union() {
    // main body
    translate( [ -77 , -4.5 , 0 ] ) cube( [ 155 , 59.8 , 2 ] ); 
    translate( [ -77 , -4.5 , 0 ] ) rotate([35,0,0]) cube( [ 155 , 2 , 20.08 ] );
    translate( [ -77 , -14.7 , 14.2 ] )  cube( [ 155 , 2 , 11.8 ] );
    translate( [ -77 , 54 , 0 ] ) cube( [ 155 , 2 , 17 ] );
    
    // M3 hole body
    translate( [ 73.5 , 43.3 , 0.5 ] ) rotate([0,0,90])  cylinder( h = 14, r = 4, $fn=6);  
    translate( [ -72.5 , 43.5 , 0.5 ] ) rotate([0,0,90])  cylinder( h = 14, r = 4, $fn=6);  
    
}
translate( [ -61.5 , 1 , 1.2 ] ) cube( [ 98.5 , 42 , 10 ] );  // LCD window
translate( [ -54.5 , 8 , -1 ] ) cube( [ 85 , 30.5 , 10 ] );  // LCD window


// buzzer holes
translate( [ 55 , 1.5 , -1 ] ) cube( [ 1.3 , 4 , 10 ] );  
translate( [ 57 , 1.5 , -1 ] ) cube( [ 1.3 , 4 , 10 ] );  
translate( [ 59 , 1.5 , -1 ] ) cube( [ 1.3 , 4 , 10 ] );  
translate( [ 61 , 1.5 , -1 ] ) cube( [ 1.3 , 4 , 10 ] );  
translate( [ 63 , 1.5 , -1 ] ) cube( [ 1.3 , 4 , 10 ] );  
translate( [ 65 , 1.5 , -1 ] ) cube( [ 1.3 , 4 , 10 ] );  
translate( [ 67 , 1.5 , -1 ] ) cube( [ 1.3 , 4 , 10 ] );  

// buzzer holes corners
translate( [ 66.25 , 1.5 , -0.5 ] ) rotate([0,45,0]) cube( [ 2 , 4 , 2 ] );  
translate( [ 64.25 , 1.5 , -0.5 ] ) rotate([0,45,0]) cube( [ 2 , 4 , 2 ] );  
translate( [ 62.25 , 1.5 , -0.5 ] ) rotate([0,45,0]) cube( [ 2 , 4 , 2 ] );  
translate( [ 60.25 , 1.5 , -0.5 ] ) rotate([0,45,0]) cube( [ 2 , 4 , 2 ] );  
translate( [ 58.25 , 1.5 , -0.5 ] ) rotate([0,45,0]) cube( [ 2 , 4 , 2 ] );  
translate( [ 56.25 , 1.5 , -0.5 ] ) rotate([0,45,0]) cube( [ 2 , 4 , 2 ] );  
translate( [ 54.25 , 1.5 , -0.5 ] ) rotate([0,45,0]) cube( [ 2 , 4 , 2 ] );  

// knob hole
translate( [ 62.5 , 21 , -1 ] ) cylinder( h = 10, r = 6, $fn=30);
translate( [ 62.5 , 21 , -1.2 ] ) cylinder( h = 2, r1 = 7, r2 = 6, $fn=30);

// reset button cutout
translate( [ 44 , 26 , -1 ] ) cube( [ 1 , 6 , 9 ] );  
translate( [ 48 , 26 , -1 ] ) cube( [ 1 , 2.5 , 9 ] );  
translate( [ 68.5 , 36 , -1 ] ) cube( [ 1 , 8 , 9 ] );  
translate( [ 56 , 43 , -1 ] ) cube( [ 13.5 , 1 , 9 ] ); 
translate( [ 50.5 , 30 , -1 ] ) cube( [ 13 , 1 , 9 ] ); 
translate( [ 44.7 , 31.28 , -1 ] ) rotate([0,0,45]) cube( [ 17 , 1 , 9 ] );  
translate( [ 63.5 , 30 , -1 ] ) rotate([0,0,45]) cube( [ 8.5 , 1 , 9 ] );  
translate( [ 48.7 , 27.8 , -1 ] ) rotate([0,0,45]) cube( [ 3.55 , 1 , 9 ] );

// rear support cutout
translate( [ -64.5 , -12.7 , 14 ] ) cube( [ 10 , 3 , 16 ] );  
translate( [ 55.5 , -12.7 , 14 ] ) cube( [ 10 , 3 , 16 ] );  

}
}

module pcb_clip(){
    difference(){
    union(){
    translate( [ -3 , -12 , 17.5 ] ) cube( [ 7 , 4 , 5 ] ); 
    translate( [ -3 , -10.6 , 12.5 ] ) cube( [ 1 , 2.6 , 7 ] );  
    translate( [ 3 , -10.6 , 12.5 ] ) cube( [ 1 , 2.6 , 7 ] );  
        }
    translate( [ -4 , -8 , 18.5 ] ) rotate([30,0,0]) cube( [ 10 , 6 , 6 ] );  
   
    translate( [ 2.5 , -12 , 14.5 ] ) cube( [ 1 , 4 , 0.2 ] );  
    translate( [ -2.5 , -12 , 14.5 ] ) cube( [ 1 , 4 , 0.2 ] );  
    translate( [ 2.5 , -12 , 17.3 ] ) cube( [ 1 , 4 , 0.2 ] );  
    translate( [ -2.5 , -12 , 17.3 ] ) cube( [ 1 , 4 , 0.2 ] );          
}
}


module lcd_cover() {

difference()
{
union()
{

pcb_clip();

main_body();
// reset button
translate( [ 62.5 , 37.3 , 0 ] ) cylinder( h = 7.2, r = 3.5, $fn=30); 

//left side
translate( [ -77 , -14.7 , 0 ] ) cube( [ 1.5 , 70.7 , 26 ] );  
translate( [ -76.5 , -15 , 0 ] ) cube( [ 4 , 70 , 14.6 ] );  

//right side
translate( [ 76.5 , -14.7 , 0 ] ) cube( [ 1.5 , 70.7 , 26 ] ); 
translate( [ 73.5 , -14 , 0 ] ) cube( [ 4 , 70 , 14.5 ] );  

//rear side reinforcement
translate( [ -54.5 , -11.7 , 8 ] ) cube( [ 110 , 4 , 6.5 ] );  
translate( [ 65.5 , -11.7 , 8 ] ) cube( [ 12 , 4 , 6.5 ] );  
translate( [ 65.5 , -13 , 14 ] ) cube( [ 12 , 2 , 12 ] );  
translate( [ -76.5 , -11.7 , 8 ] ) cube( [ 12 , 4 , 6.5 ] );  
translate( [ -76.5 , -14.7 , 14.5 ] ) cube( [ 12 , 4 , 11.5 ] );  
translate( [ -44 , -14.7 , 14.5 ] ) cube( [ 89 , 4 , 11.5 ] );  
translate( [ -43.5 , -10.7 , 15 ] ) rotate([90,0,0]) cylinder( h = 2, r = 11, $fn=60);  
translate( [ 44.5 , -10.7 , 15 ] ) rotate([90,0,0]) cylinder( h = 2, r = 11, $fn=60);  


//front left side reinforcement
difference()
{
    union(){
        translate( [ -77 , 41.3 , 0 ] ) cube( [ 15 , 14 , 25 ] );  
        translate( [ -77 , 46.3 , 14 ] ) cube( [ 15 , 9 , 3 ] );  
        }
    translate( [ -64.5 , 40 , -3 ] ) cube( [ 4 , 8 , 40 ] );  
    translate( [ -75.5 , 40.3 , 14.5 ] ) cube( [15 , 6.5 , 25 ] ); 
}


//front right side reinforcement
difference(){
translate( [ 38 , 41.2 , 0 ] ) cube( [ 40 , 14 , 26 ] );  
translate( [ 55 , 44.5 , 0 ] ) cube( [ 10.5 , 3.7 , 30 ] );  
translate( [ 44 , 39.5 , 0 ] ) cube( [ 25.5 , 5 , 30 ] );  
translate( [ 35 , 39.3 , 14.5 ] ) cube( [ 42.5 , 7 , 15 ] );  

translate( [ 49 , 43.2 , 25 ] ) rotate([0,60,0]) cube( [ 12 , 5 , 10 ] );  
    

}
}

// SD card opening
translate( [ -80 , 9 , 14.5 ] ) cube( [ 10 , 28 , 6 ] );  

// front and rear angle
translate( [ -81 , -9.3 , -17 ] ) rotate([35,0,0]) cube( [ 164 , 14 , 54.08 ] );  
translate( [ -78 , 72.7 , -3 ] ) rotate([45,0,0]) cube( [ 160 , 14 , 54.08 ] );  

// M3 screw thread
translate( [ 72.7 , 43.2 , 3 ] ) cylinder( h = 20, r = 1.4, $fn=30);  
translate( [ -72.5 , 42.7 , 3 ] ) cylinder( h = 20, r = 1.4, $fn=30); 
translate( [ 72.7 , 43.2 , 14 ] ) cylinder( h = 1, r1 = 1.4, r2=2, $fn=30);  
translate( [ -72.5 , 42.7 , 14 ] ) cylinder( h = 1, r = 1.4, r2=2, $fn=30); 

lcd_text(0.8);

// front cleanup
translate( [ -100 , -64 , 0 ] ) cube( [ 200 , 50 , 50 ] ); 

// corners
translate( [ 76 , -5 , -1 ] ) rotate([0,45,0]) cube( [ 5, 80, 5 ] );  
translate( [ -82 , -5 , -1 ] ) rotate([0,45,0]) cube( [ 5, 80, 5 ] );  
translate( [ -82 , 58 , -4 ] ) rotate([45,0,0]) cube( [ 200, 5, 5 ] );  
translate( [ -77 , 54 , -4 ] ) rotate([0,0,45]) cube( [ 5, 5, 50 ] );  
translate( [ 78 , 54 , -4 ] ) rotate([0,0,45]) cube( [ 5, 5, 50 ] );  
translate( [ 78 , -19 , -4 ] ) rotate([0,0,45]) cube( [ 5, 5, 50 ] );  
translate( [ -77 , -19 , -4 ] ) rotate([0,0,45]) cube( [ 5, 5, 50 ] );  

// LCD corners
translate( [ -54.5 , 9.5 , -5.2 ] ) rotate([45,0,0]) cube( [ 85 , 5 , 5 ] );  // LCD window
translate( [ -54.5 , 37 , -5.2 ] ) rotate([45,0,0]) cube( [ 85 , 5 , 5 ] );  // LCD window

rotate([35,0,0]) translate( [ -78 , -7 , -4 ] ) rotate([0,0,45]) cube( [ 5, 5, 50 ] );  
rotate([35,0,0]) translate( [ 79 , -7 , -4 ] ) rotate([0,0,45]) cube( [ 5, 5, 50 ] );  

}
}

module colortext() {
    lcd_text(0.6);
}

module lcd_text(th) {

// HARIBO Edition text
translate([-54,52,0.6]) rotate([180,0,0]) linear_extrude(height = th) 
{ text("HARIBO",font = "BPreplay:style=Bold", size=10, center=true); }

translate([-56.5,52,0.6]) rotate([180,0,270]) linear_extrude(height = th) 
{ text("3030",font = "BPreplay:style=Bold", size=5.5, center=true); }

translate([63,0,0]) {
translate([-67,52,0.6]) rotate([180,0,0]) linear_extrude(height = th) 
{ text("EDITION",font = "BPreplay:style=Bold", size=7, center=true); }

// Line over small text
translate( [ -66 , 41.5 , 0 ] )  cube( [ 32 , 1.6 , th ] );  
translate( [ -66 , 42.3 , 0 ] ) cylinder( h = th, r = 0.8, $fn=30);  
translate( [ -34 , 42.3 , 0 ] ) cylinder( h = th, r = 0.8, $fn=30);  
}

// HARIBO Number
if (haribo_number > 0) {
  translate([-73,5,0.6]) rotate([180,0,0]) linear_extrude(height = th) 
{ text(str("#",haribo_number),font = "BPreplay:style=Bold", size=6, center=true); }
}

// X sign on reset button
translate( [ 63 , 34 , 0 ] ) rotate([0,0,45]) cube( [ 2, 8, th ] );  
translate( [ 57.5 , 35.5 , 0 ] ) rotate([0,0,-45]) cube( [ 2, 8, th ] );  
}

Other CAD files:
STL/optional/16mm Tnut Spacing/1x_z_motor_mounts_16mm.stl
STL/optional/MK2S-modified-y-belt-holder-3mm-taller.stl
STL/square_slot_extrusions/1x_y_idler.stl
STL/1x_power_supply_mounts.stl
STL/10x_cable_clips.stl
STL/1x_filament_spool_and_guide.stl
STL/1x_lcd_mount_extended_pcb_ears.stl
STL/1x_rambo_mount.stl
STL/1x_y_idler.stl
STL/1x_y_motor_mount.stl
STL/1x_z_rod_holders.stl
STL/2x_t_bracket.stl
STL/3x_y_bearing_housing.stl
STL/4x_y_rod_holder.stl
STL/6x_l_bracket.stl
STL/7x_end_cap_3_leg.stl
STL/mmu/1x_superswitch_mount.stl
STL/optional/16mm Tnut Spacing/1x_y_motor_mount_16mm.stl
STL/optional/16mm Tnut Spacing/6x_L_bracket_16mm.stl
STL/optional/1x 67.75mm Jig.stl
STL/optional/1x_LRS-350_12_bottom.stl
STL/optional/1x_LRS-350_12_top.stl
STL/optional/1x_aftermarket_y_carriage_raiser.stl
STL/optional/1x_fan-nozzle-haribo.stl
STL/optional/1x_lcd_cover.stl
STL/optional/1x_lcd_cover_text.stl
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

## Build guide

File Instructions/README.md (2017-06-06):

# Instructions

## Important measurements

The only one that you need to worry about is the spacing of the left y rod holders.

On the reference build, each left y rod holder is 67.75mm from the edge of the extrusion.

Ensure the front and back measurements of the left side are the same.  Then using the the bearings and the y carriage, ensure the right side y rods are parallel and the y carriage ride smoothly.  if needed adjust position of the bearing holders so that the y carriage slides smooth.

## Guidelines

- build on a level hard surface and ensure the frame is square as you tighten the frame bolts.
- when installing the frame braces, tighten them but don't go hulk strength and crack them.
- I found fender washer for the y carriage bolts spread the load and help maintain consistent contact
- make sure you use the correct length M6 screws, most pieces use M6 x 12 but others use M6 x 14, 
  - M6 x 12mm screws should be used for the parts that have recessed holes. Namely: Y idler and motor holder, the Rambo mount
  holder and the Z Rod Holders
  - M6 x 14mm screws with washer should be used on L and T brackets
- the firmware changes are optional. you can make this work without making any changes by moving the gantry so tha the nozzle is 210mm from the print bed

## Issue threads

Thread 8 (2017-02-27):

Varying M6 Screw Lengths for Printed Parts

ar-o-be, 2017-02-27:
# What
Some printed parts require M6x14, some require M6x12 screws. It's not defined anywhere which parts require which screws.

# Proposed Solution
Either one of these two solutions would suffice:

1. The BOM and Assembly Instructions should carefully note the different lengths required for each part.

*OR*

2. The STL files should be updated to be slightly "beefier" so that we can standardize on the M6x14 screws, and eliminate the need to purchase M6x12.

**Known Parts Which Require M6x12**
- [1x_rambo_mount.stl](https://github.com/PrusaMK2Users/3030_Haribo_Edition/blob/master/STL/1x_rambo_mount.stl) **REQUIRES 2**
- [1x_y_motor_mount](https://github.com/PrusaMK2Users/3030_Haribo_Edition/blob/master/STL/1x_y_motor_mount.stl)

Tigwin, 2017-03-01:
I vote for beefier whenever possible. It adds strength in addition to less checking of screw lengths during the install.

jtktam, 2017-03-01:
some parts there is no clearance for beefy parts and we need to use 12mm

check the z rod holders too

Tigwin, 2017-03-03:
z rod holders were fine for me. just the rambo and y motor mount so far.

jtktam, 2017-03-06:
@ar-o-be and i will be working on updating the hardware count and maybe add in location of each bolt as we get the documentation going

jrezin, 2017-07-19:
all the printer can be currently build without ANY m6x14. besides that, this specific size cannot easily found. it is probably better just get ride of it and use m6x12 and m6x16 (easily found all around the world) instead of using m6x14 as standard.

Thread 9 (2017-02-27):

Need Proper Assembly Instructions

ar-o-be, 2017-02-27:
We need explicit step-by-step instructions for assembly from scratch (using an upgrade kit from Prusa) *AND* assembly using an existing MK2 as a donor.

stevendpclark, 2017-02-27:
When my MK2 upgrade kit, ordered last week so I have a while to go, arrives I can help out with this effort, either by starting, updating and/or reviewing the document

jtktam, 2017-03-06:
@stevendpclark it would be great if you can help out

stevendpclark, 2017-03-15:
I've started documenting my build progress within the wiki of my github clone:
https://github.com/stevendpclark/3030_Haribo_Edition/wiki/AssemblyInstructions

Work in progress, and I'm more then willing to let it go if ar-o-be is planning better pictures or would like something else.

stevendpclark, 2017-04-18:
Sorry about the delay, I've had various things come up the last month sadly.

I'm finally ready to get back to documenting my build but was wondering if this is still a desirable within the project considering the news about the upgrade kits?

JohnOCFII, 2017-04-18:
Welcome back!  I think more clear, simple documentation is still needed.  You and @ar-o-be might be able to divide and conquer!

zsocietyGithub, 2019-01-14:
i plan to Scratch-Build this haribo version,  i have issu about dimenson of the frame profile. can i use this manual instruction to assambly the profile from rebeliX [http://reprap4u.cz/navod-na-stavbu-3d-tiskarny-rebelix/](url) this frame using same profile 3030 and use 3d print part from haribo?.

C4, 2019-01-23:
I've used this guide from Zaribo to assemble my Haribo 3030 build. Instructions are pretty good. Reminds me of Prusa / iFixt style instructions. http://zaribo.org/blog/zaribo-manual-assembly-of-the-frame/

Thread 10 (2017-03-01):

LCD Cover Model Issues

ar-o-be, 2017-03-01:
The "HARIBO" LCD Cover has several known issues:
- "X" button does not properly depress. There is a block preventing the button from moving.
- If you measure the recess on the sd-card side, you’ll probably find it’s 14.5mm.  The one on the other side is 12.5, as is the one on the original prusa LCD cover.
- The opening of the LCD cover is larger than it needs to be. Bottom of opening aligns correctly with LCD, but the top extends too far.

ar-o-be, 2017-03-29:
Fixed with #18

Closed 2017-03-29.

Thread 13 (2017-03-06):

Source files

syky27, 2017-03-06:
Why there are no source files for parts?

This is not how open-source works...

Kinda sux, when you need to modify stuff.

jtktam, 2017-03-06:
i starred with stl files from průša and the mk2-x project and the resultant stl files are all here.  there is no source files being withheld.  maybe your definition of open source is having step files etc? almost every other printer project only release stl files

ryanneufeld, 2017-03-19:
@syky27 More specifically:

As these parts were made using TinkerCAD, and online CAD package, there are no source files. Only the STL outputs.

The STL are in effect, the source.

Closed 2017-03-06.

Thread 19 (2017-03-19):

Ease of getting the distances correct for the connection of vertical extrusions

mrjohnc, 2017-03-19:
An common problem for the Mk2 design is getting the distance correct for attaching the vertical and horizontal sections. Can I suggest adding a 3D printed spacer to the design to take the guess work out? The spacer would fit in the groove behind the vertical section.

Thanks

jtktam, 2017-03-19:
the design of the haribo does not need spacers because there is no way for you to do it wrong.. the distance is governed by the through hole in the extrusions. if it's unclear please join slack chat and look for jtktam

Closed 2017-03-19.

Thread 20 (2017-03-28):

LRS-350-12 Meanwell PSU Cover Enhancements

ar-o-be, 2017-03-28:
Make some changes to the Meanwell LRS-350-12 cover to allow the cable holes to be larger.

As noted by @JohnOCFII in the [#16](https://github.com/PrusaMK2Users/3030_Haribo_Edition/pull/16).

> I'd request the hole for the cables be made larger (or Joseph suggested additional holes) to hold larger diameter cables and/or additional cables. I'd suggest making the opening twice as tall and twice as wide (or two holes with similar total opening space).

ar-o-be, 2017-03-29:
Fixed with #21

Closed 2017-03-29.

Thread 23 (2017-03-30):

Block spacing for Tnuts on L and T brace possibly needs widening.

davvyk, 2017-03-30:
The current spacing between blocks on the T and L braces only allows space for the 14mm Tnuts purchased from Misumi.

As these are unavailable to many people outside the states and the 14mm size seems to be unique to Misumi it has been suggested a wider spacing of 16mm be used as this would let people use the commonly available 15.8mm Tnuts.

I knocked up STL files to print myself if you want them, they are linked below.

Thanks.

https://www.dropbox.com/s/ams92czv7z1n96p/16mm%20L%20Brace.stl?dl=0

https://www.dropbox.com/s/fff85nx6iuj757r/16mm%20T%20Brace.stl?dl=0

ar-o-be, 2017-03-30:
@davvyk Would you mind submitting a PR with the STL files and adding a description to the README about the part and why it's useful? Let me know if you need help with PR and I'd be glad to help out!

davvyk, 2017-03-30:
Hi Arobe.

Yeah if you could give me a pointer on doing a pull request. Never really done a ton of work in git before so dont want to go causing any issues.

Thanks

JohnOCFII, 2018-02-10:
Does this issue still remain, or can this Github issue be closed?

dino340, 2018-05-19:
Opened PR to add davvyk's models to the Optional folder, need to verify if this issue extends to other models.

JohnOCFII, 2018-05-22:
Issue resolved by @dino340 PR.  If this needs to be extended, please re-open.

Closed 2018-05-22.

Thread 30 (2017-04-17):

Precision Linear Shaft and Bearing Questions

doubleoerik, 2017-04-17:
First question/comment is regarding the Misumi shaft. The part number you specify of PSFG8 is a 8mm Outside Diameter (OD) 1045 carbon steel hard chrome plated shaft with a diametrical tolerance of "f8" which means the diameter will nominally be -0.013mm to -0.035mm less than 8mm. It might be worth noting for the folks using the Misumi LMU8 bearings that the Inside Diameter (ID) tolerance on the bearing is 0mm to -0.009mm and the Misumi technical documentation states that they recommend a shaft with a "g6" tolerance of -0.005mm to -0.014mm (https://us.misumi-ec.com/pdf/fa/2012/p1_0265.pdf). I suspect the shaft you selected is appropriate for the IGUS DRYLIN bushings you call out in your BOM but it seems like folks using LMU8 bearings should consider using the equivalent "g6" tolerance shaft part number PSFJ8 (52100 bearing steel shaft that is induction hardened and is also hard chrome plated). Does that make sense? I'm definitely not an expert so please set me straight if I'm missing something.

The second question/comment is regarding the bearings. The baseline Prusa i3 mk2 design essentially uses back-to-back bearings on the X and Z axis (2 on X as part of the extruder assembly and 2 on each Z carriage). Is there any reason not to go with double bearings (LMUW8) in these three locations instead of sticking with the back-to-back configuration? Perhaps you didn't do this because the IGUS DRYLIN bushings don't have a double length option? We're 3D printing upgraded parts anyway so it seems like a true double bearing would be a better option for these locations. Again, I'm no expert so please educate me if I'm missing something.

Thanks and awesome work on this stuff!

JohnOCFII, 2017-04-17:
@doubleoerik - Interesting note on the LMU8 and the shaft diameter.  I ordered the LMU8 bearings, but assumed similar 8mm tolerances to the default LM8UU bearings from Prusa that shipped with the MK2.

The primary developer of the Haribo 3030 ( @jtktam ) suggested that I try the double-length Misumi bearings in Z - I don't recall if he was also OK with using them in the X carriage.  But - as you point out, I wonder if there will be a tolerance issue.

You may get more discussion going in the Slack group.  If you aren't already a member, I can send you an invitation.

John

doubleoerik, 2017-04-17:
An invitation would be great - thanks!

On Mon, Apr 17, 2017 at 12:42 PM, JohnOCFII <notifications@github.com>
wrote:

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

JohnOCFII, 2017-04-17:
Sure thing, @doubleoerik - I need your email address -- I don't see it in your GitHub profile.

doubleoerik, 2017-04-18:
doubleoerik@gmail.com

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

doubleoerik, 2017-09-12:
Quick follow-up on this - I went ahead and replaced the back-to-back bearings on my z-carriage with double length Misumi LMUW8 bearings. I had to design new z-carriage brackets as I wanted a precision fit for the 45mm long Misumi bearings and I also wanted to incorporate anti-backlash spring loaded nuts into the bracket. It then made sense to redesign the rest of the z-axis brackets (top and bottom) so everything played together nicely but that's for another thread. I've been printing with this setup for months and couldn't be happier with it so anyone out there hesitant to do this upgrade - it's perfextly fine.

I also replaced the back-to-backs on the extruder with a single double bearing. I had to design a adapter to keep the bearing centered in the OEM x-carriage body but otherwise this is working great as well. Next on my list is to mess with the bed as it's not proportionally as rigid/sturdy as the rest of he machine has become. The first thing I may try to do is to replace the single left side bearing with a double length bearing. I suspect Joseph designed it this way so it isn't over-constrained but I'm hopeful I can get it lined up well and bank on the compliance of the system to absorb any overconstraint. The goal is to eliminate the rocking that can occur on the side of the bed with the single bearing.

JohnOCFII, 2017-09-13:
Great info, @doubleoerik - you might also want to post this in the Haribo3030 channel on Mattermost.  (the community moved from Slack a few months ago.  https://3dprinting.community/login

Closed 2017-06-16.

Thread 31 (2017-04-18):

Incorrect link in BOM

Cova, 2017-04-18:
The BOM indicates a requirement for 2x "GT2 16T pulley" - and provides a link to purchase them from RepRap Champion.  However the link sends you to a page for a 16T GT2 Idler with ball-bearings having a 3mm bore.

I believe the correct link should be:
https://reprapchampion.com/collections/mechanical-components/products/high-quality-gt2-16t-aluminum-timing-belt-pulley-reprap-3d-printer-prusa-i3

mihec87, 2017-05-16:
Edited and added correct link..

Closed 2017-06-16.

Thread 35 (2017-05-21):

Firmware says to change encoder steps, but ...

Tigwin, 2017-05-21:
those values are already the default in the current version of the firmware. (.11)

JohnOCFII, 2017-05-22:
3.0.11 was just released two days before your message.  We just don't move that fast around here -- day jobs, you know. :)

Thanks for the point out.

Tigwin, 2017-05-22:
I'm aware. Just making a note its out of date now.  Its one less thing to configure.

Closed 2017-05-22.

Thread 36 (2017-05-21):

HPI Blitz / Firestorm Titanium Idler Gear Shaft 5x16m #104138 availability

mihec87, 2017-05-21:
Trying to source HPI Blitz / Firestorm Titanium Idler Gear Shaft 5x16m #104138( HPI part number #104138) shows that this part is discontinued and is hard to get by...
After some digging around i came to part witch is the same dimension(5x16mm) but it is not from titan. #86947 - IDLER GEAR SHAFT 5x16mm https://www.hpiracing.com/en/part/86947 if we search for hpi 86947 on ebay/google we get much more hits.. I think it is equal replacement...

Tigwin, 2017-05-21:
I can tell you right now that printing this part out of PETG / PLA works great. I had my doubts, but its working fine.

hungtru, 2017-10-30:
can you point me to where you found the stl for it?

dino340, 2018-01-27:
You can easily make one in any modeling software including tinkercad by making a cylinder with a base diameter of 5mm and a height of 16mm.

JohnOCFII, 2018-02-10:
Updated parts also now on BOM.

Closed 2018-02-10.

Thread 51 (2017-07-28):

Error in X Motor Mounts

Richardgriff, 2017-07-28:
I have been having some problems with printing the X motor mount and everything I tried resulted in the part breaking.

On looking at the file in mesh mixer I found that there appears to be an error in the model that appears in exactly the same location as the part failures.

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

Please can someone tell me how to fix this or fix the model for me.

Thanks

Richard

jtktam, 2017-07-28:
i will have a look at the model.  the part prints fine for most of the folks who been using it.  what slicer you using?

jtktam, 2017-07-28:
[Z motor mount v2.zip](https://github.com/PrusaMK2Users/3030_Haribo_Edition/files/1183463/Z.motor.mount.v2.zip)

can you try this one and see if it solves your issue

the 0.1 offset shouldn't make the part weak, so i suggest you look at your print settings to ensure it's not causing the break

Richardgriff, 2017-07-28:
Hi tam,

Thanks for the quick reply. I am using cubicon creator which I think is based on a version of cura.. I will have a go printing the file you have send over and will let you know.

I have been browsing though the commits and found that the error seems to have crept in when the model was widened for more clearance and the model rotated.

Would printing the original model cause any issues

Richard

Richardgriff, 2017-07-28:
Using a Cubicon Style

Print settings are as follows
ABS @ 260 degrees
Bed temp 110
0.2mm Layer Height
0.8mm Wall thickness
4 Top and Bottom Layers
30% infill
Cooling Fan OFF

jtktam, 2017-07-28:
let me know if the new model fixed your issue, i will commit it to the branch once it's confirmed

the slight shift of 0.1 shouldn't cause the issue you are seeing.. i think the transition from the large base to the vertical member might be your weak spot..

i have no experience with abs, i printed most of the parts with petg

Richardgriff, 2017-07-31:
Hay tam,

I tried printing the v2 version and again encountered the problem but slightly less. I passed the stl though several different slicers
The slicers I used where

Cubicon creator
Sli3r prusa
Sli3r normal
Cura 2.6

Viewing the gcode I found that the cubicon creator is the only on to pick up on the flaw and does not produce the layers as you would expect. All other slicers produce a simalr gcode.

The problem I have is that I need to use cubicon creator as it add custom gcode and setting and crc checks them to prove they have been produced using the cubicon creator tool. This is one of the main reason I was trying to switch to an open source printer.

So I ask kindly please can you upload a version with this fix. I know that for 99.9% of the time nobody would see this issue but I would really like to get my printer up and running and these are the final parts

Thanks

Richard

JohnOCFII, 2018-02-10:
Does this issue still remain, or can this Github issue be closed?

w0dash, 2021-01-22:
This issue remains until today (see the blue overhang):

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

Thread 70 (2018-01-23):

M6 nuts not on BOM

terrag42, 2018-01-23:
I'd like to know how many M6 nuts are required, they are not on the BOM. I see that there are 12+54+4 M6 bolts, so do I need 70 nuts?

jtktam, 2018-01-23:
we don't use m6 nuts.. the t-nuts are listed and they go into the extrusion channels

Closed 2018-02-10.

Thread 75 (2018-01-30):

source files

tcurdt, 2018-01-30:
It seems like this repo only has the STL files.
Where are the source files?
What am I missing?

Tigwin, 2018-01-30:
Welcome to 3d printing. You'll find that most projects release stl files, Prusa included. Anything based on a stl, would obviously also be a stl.

tcurdt, 2018-01-30:
@Tigwin Indeed everything gets exported to STL in the 3d printing world - but hardly anyone uses that as the source format.

Prusa uses OpenSCAD to model the parts and then exports them to STLs. [The scad files are also available](https://github.com/prusa3d/Original-Prusa-i3/tree/MK2/Printed-Parts). Other projects use Fusion360 or Blender to model their parts.

SkyDriver2k4, 2018-02-10:
the most parts are on jtktams tinkercad. my own files are on fusion. so if you wish to change anything or get access to it. just ask for it on mattermost ~haribo3030 channel.

Closed 2018-02-10.

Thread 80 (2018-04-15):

Can we get the original CAD files?

metacollin, 2018-04-15:
Providing a bunch of .STL files is analogous to providing binaries alone.  Where are the .scad files that were used to generate the STL files?  Or, if OpenSCAD wasn't used, where are the original design files in whatever CAD program that was originally used?

You license this under the GPL, but in every way that matters, this project is closed source.  It is definitely arguable that this repo is in violation of the GPL, as the files needed to generate the .STL files are not available, but you've clearly used some of the prusa .scad file code in parts to create new .STL file variations for this mod.

Case in point:  there is an error in the L and T brackets.  In the T bracket, two of the holes have a very low poly count set (which would only be an issue for something created in OpenSCAD...so where is the .scad _**source code?**_), while all of the holes are like this in the L bracket.

Since this project is not open source, I cannot easily fix what should be a trivial change.  I would change one '$fn =' statement and be done.  But I can't, because you haven't included the source.  I also can't do a pull request of said change and contribute to the repository.

My only option would be to recreate the .scad source independently which will not necessarily be the same code at all, and only produce something functionally equivalent.

This is how you can tell if something isn't open source, if people have to literally do the exact same thing as the reason behind linux even existing (it was to make a functional clone of unix, back when unix was closed source), then it isn't open source.

I request the inclusion of the CAD source files, or links to non-private tinkercad projects (or whatever else cloud-based service that might have been used), for every .STL included in this repo that is in some way derived from the original Prusa design.  At the very least to be in the spirit of the GPL, if not in actual compliance with it.

I know the people maintaining this repo may not have these files themselves.  It it still your responsibility to contact the people that do, and acquire them for the inclusion in this repository.

Tigwin, 2018-04-15:
Hey smart guy. What if the designs were made in tinkercad, and they export as stl's?

metacollin, 2018-04-15:
Then do this: https://metacollin.com/screens/upshot_fFHvB2p4.png

And provide links in a text file.

Tigwin, 2018-04-15:
You'll still just get a stl from it.

metacollin, 2018-04-15:
No, you get a copy of the actual tinkercad project in tinkercad, allowing you make edits to the original raw objects, which you can export as an STL.

I would be able to ungroup the L bracket for example, find the low poly cylinder holes, edit them, regroup, and rexport a new STL.

I cannot do this as you've not provided me a means to, which you are legally obligated to do due to the GPL.

metacollin, 2018-04-15:
Here, maybe this will make it a little clearer:  If I have a link to a public Tinkercad project, I can click 'copy and tinker', and I get all the original individual objects used to create the model, grouped or ungrouped, and can easily edit them.  https://metacollin.com/screens/upshot_ysrrJqiv.png

On the other hand, I lose all of this information and cannot easily make any changes if I instead simply import a raw .stl file into Tinkercad: https://metacollin.com/screens/upshot_kEdUsQXH.png

Its analogous to how you can, technically, edit the raw machine code of a .exe, but that isn't the same as having access to the original means of editing and design, which in the case of a .exe, is the source code.  In this case, it would be tinkercad projects, or fusion 360 projects, or .scad files, or what have you.  Even if they cannot be directly included in the project repo, the means to acquire them (like on tinkercad) in a README somewhere would be enough for compliance.  And extremely helpful.

Sorry, I probably am not helping to motivate the powers that be.  This project is awesome, I love my 3030 mod, and i've made my own MK2.5/MK3-ish version with an Einsy.  I was just somewhat disappointed to discover that there were no .scad (or whatever) files, and I had just assumed they were there until I actually needed to edit or 'remix' something.

JohnOCFII, 2018-04-15:
Just to confirm.  The Haribo 3030 parts were designed in TinkerCAD.  There is no other CAD source.

metacollin, 2018-04-15:
Excuse me, we both know this is nonsense.  You can provide links to the tinker cad projects and make them public,

jtktam, 2018-04-15:
i choose not to make my tinkercad projects public, the stl files is what i started with and stl file plus the bom and documentation is what i am releasing.  it does not, as wrongfully alleged by you, violate the gpl and it’s not the same as binary files and source code..

also this design has zero to do with prusa.. so stop trying to make it an issue

Closed 2018-04-15.

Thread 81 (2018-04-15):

Please provide links to public Tinkercad projects for the .stl files.

metacollin, 2018-04-15:
Here, maybe this will make it a little clearer: If I have a link to a public Tinkercad project, I can click 'copy and tinker', and I get all the original individual objects used to create the model, grouped or ungrouped, and can easily edit them. https://metacollin.com/screens/upshot_ysrrJqiv.png

On the other hand, I lose all of this information and cannot easily make any changes if I instead simply import a raw .stl file into Tinkercad: https://metacollin.com/screens/upshot_kEdUsQXH.png

I wish to fix an issue with the poly count of the L and T brackets, as well as make other improvements without having to manually recreate the model (which in some cases isn't even possible to do), by hand.

There is no issue preventing you from doing this.  Refusing to is both against the spirit of open source, and in violation of the GPL which this project is subject to.  Please include links to the original tinkercad projects, which have been made public (goto settings -> change private to public).  This allows people to 'copy and tinker' within tinkercad.  Whether or not there exist actual cad files is irrelevant to the compliance of the GPL and there is nothing preventing you from doing this.  Tinkercad has the ability to share projects between users, so please share the Haribo 3030 projects.

jtktam, 2018-04-15:
1. this project has nothing to do with prusa research. none of their files were used and if they were used we asked you to print them from THEIR source files
2. the input files this was based from us from the mk2-x project which has stl as the “source files”
so this continues the trend of that project
3. i released the stl, the complete bom and instructions, which is way more than required by any license..  and i have been a proponent of OSHE.. so don’t accuse me of allege infringements
4. in the future you will find that you get more bees win honey than vinegar.  if you contacted me i would have shared it personally above and beyond what is required .. and others have contributed this way.

jtktam, 2018-04-15:
and i am not obliged by any license to release files in the format that you feel is needed or on any specific platform/package you feel.. what if i drew the first draft with pencil and paper.. you expect that too?

btw yes i did do it on paper

Closed 2018-04-15.

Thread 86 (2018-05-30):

Wrong Part # for the Extruder Springs in the BOM

MoshiBin, 2018-05-30:
The BOM lists "HFS6-3030-200-Z8-XA15" as the Misumi part number of the extruder springs - but that's incorrect. The listed part number is for one of the spool holder extrusions.

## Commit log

2017-01-10 Initial set of STL files
    this is the initial set of STL files as per v1.0 build
    [1x_lcd_mount_extended_pcb_ears.stl, 1x_power_supply_box.stl, 1x_power_supply_mount.stl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]
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2017-01-11 initial spool holder
    it's still a work in progress, the spool holder and filament guide will
    work for now. will need to raise it by 20mm+ so the filament enters the
    guide at a good angle
    [1x_filament_spool_and_guide.stl]
2017-01-12 new spool holder and guide
    [1x_filament_spool_and_guide.stl]
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2017-01-12 strengthen the z rod holder
    [1x_z_rod_holder.stl]
2017-01-15 y rod holder qty changed
    [4x_y_rod_holder.stl]
2017-01-15 rambo mount and BOM updated
    m6 x 14 <-> m6 x 10
    bigger footprint for rambo mount
    [1x_rambo_mount.stl]
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2017-01-17 Fan nozzle by jonasrh
    [fan-nozzle-haribo.scad, fan-nozzle-haribo.stl]
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2017-01-19 end cap count +1
    [7x_end_cap_3_leg.stl]
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2017-01-23 added t joint and fixed hole for spool holder
    [1x_filament_spool_and_guide.stl]
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2017-01-26 stock power supply mount added
    [stock_power_supply_mount.stl]
2017-01-27 add missing y bearing housing
    [3x_y_bearing_housing.stl]
2017-01-27 stock psu mount updated
    [stock_power_supply_mount.stl]
2017-01-27 support spacing fixed
    [stock_power_supply_mount.stl]
2017-02-02 Adds HARIBO lcd cover.
    [1x_lcd_cover.stl]
2017-02-03 psu supply mount <-> aftermarket psu mount, removed user submission
    [1x_power_supply_box.stl, 1x_power_supply_mount.stl, stock_power_supply_mount.stl]
2017-02-03 clean up file names and readme.md
    [1x_fan-nozzle-haribo.scad, 1x_fan-nozzle-haribo.stl, fan-nozzle-haribo.scad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]
2017-02-03 Alternative y belt holder
    Alternative y belt holder based around the stock MK2 model, modified to fit the 3030 Haribo's dimension requirements.
    [1x_modified_stock_y_belt_holder.stl]
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2017-02-04 Rotated the part 180 degrees so it faces cooling.
    [3x_y_bearing_housing_rjzm_01_08.stl]
2017-02-05 Renamed the file so it is in the optional/ folder.
    [3x_y_bearing_housing_rjzm_01_08.stl]
2017-02-05 picky people want filename corrected
    [1x_power_supply_mounts.stl, 1x_z_motor_mounts.stl, 1x_z_rod_holders.stl]
2017-02-05 fixed 1mm too high post
    [1x_rambo_mount.stl]
2017-02-17 Shorter version of the LM8uu bearing holders.
    [3x_y_bearing_housing_lm8uu_short.stl]
2017-02-19 The shorter version, will fit (instead of the one in the spoolholder_guide.stl) next to the L-bracket on the Z-axis. This way the horizontal
    [1x_Spoolholder_L-bracket_short.stl]
2017-02-19 Shorter version, to fit the spoolholder
    The shorter version, will fit (instead of the one in the
    spoolholder_guide.stl) next to the L-bracket on the Z-axis. This way the
    horizontal part of the spoolholder will be centered on the axis and the
    filament guide will also fit perfectly.
    [1x_Spoolholder_L-bracket_short.stl]
2017-02-20 merged short l bracket to filament spool and guide
    [1x_Spoolholder_L-bracket_short.stl, 1x_filament_spool_and_guide.stl]
2017-02-20 promote optional parts
    the y belt holder and bearing housing has been promoted from optional to
    reference status
    [1x_y_belt_holder.stl, 3x_y_bearing_housing.stl]
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2017-02-20 slic3r-fied files
    slic3r seems to have a problem with these files, so @cube fixed them and
    made them available here
    [1x_power_supply_mounts-fix.stl, 1x_rambo_mount-fix.stl, 1x_y_idler-fix.stl]
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2017-02-26 Flip haribo fan nozzle 180 for printing
    The piece as originally oriented would not print properly without supports as the majority of it is in thin air. Flip the part 180 degrees for easier printing without supports.
    [1x_fan-nozzle-haribo.stl]
2017-03-01 format scad file
    - No changes to source other then formatting the module code with proper indentations.
    [1x_fan-nozzle-haribo.scad]
2017-03-02 Add a new module that flips the nozzle 180 degrees
    - Add a new module to the scad file that flips the entire part 180 degrees to generate an STL file that is immediately printable
    - Regenerate STL file based on scad file
    [1x_fan-nozzle-haribo.scad, 1x_fan-nozzle-haribo.stl]
2017-03-11 Initial design for LRS-350-12 Meanwell Power Supply cover. Use stock socket, switch and wires.
    [LRS-350-12.stl]
2017-03-15 Fixes HARIBO LCD cover issues.
    [1x_lcd_cover.stl]
2017-03-15 Fixes issue with new STL file for LCD text
    [1x_lcd_cover.stl]
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2017-03-18 Fixes table display in BOM
2017-03-23 modified z motor mount for more clearance on both sides
    [1x_z_motor_mounts.stl]
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2017-03-28 Added an extra hole to fix issue #20 and renamed the file. Also included the top bracket for the PSU.
    [LRS-350-12-bottom.stl, LRS-350-12-top.stl, LRS-350-12.stl]
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2017-04-01 Modified MK2x Y belt holder. Added 2mm on each end since some had problems with the endstop being activated. Made the screw holes the same as the stock holder to be able to use same screw lengts.
    [1x_mk2x_y_belt_holder_modded.stl]
2017-04-03 Addes M4x6mm SHBS (used for optional PSU cover) Updated screw counts for M6x14 (after adding M6x12). I know the math doesn't add up, I left extra. Fixed a few typos
2017-04-12 Adding LRS-350 cover with removable lid. Sorting table alphabetically.
    [LRS-350 Enclosure Body.stl, LRS-350 Enclosure Lid.stl]
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2017-04-16 Fixes incorrect links and removes duplicate BOM entry.
2017-05-02 Added instructions to invert the logic of the LCD wheel. Up becomes down, down become up. Like an Australian moving to North America!
2017-05-11 Add files via upload
    Thin plate to mount the original Rambo case to the aluminium extrusion. Use 2x M6x12 countersunk screws to mount the plate and the original M3 screws and nuts for the case.
    [i3 Haribo Rambo Mount Thin.stl]
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2017-06-12 Move and rename file to correct place
    [1x_i3_haribo_rambo_mount_thin.stl]
2017-06-30 mmu parts for haribo
    Remixed motor mount. Superswitch case in the style of the rambo mount.
    [e-motor-holder-haribo.stl, superswitch-case-haribo.stl]
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2017-07-05 Removing un-usable version and replacing with usable version.
    [1x_i3_haribo_rambo_mount_thin.stl, 1x_rambo_3030_adapter.stl]
2017-07-05 Add superswitch case adapter. Rename files to meet naming standards (#45)
    [1x_e_motor_holder.stl, 1x_superswitch_adapter.stl, 1x_superswitch_mount.stl]
2017-07-05 Removing un-usable version and replacing with usable version. (#44)
    [1x_i3_haribo_rambo_mount_thin.stl, 1x_rambo_3030_adapter.stl]
2017-07-05 Squashed commit of the following:
    commit c7be1d41476bd47d124dba50f2278af613e7fe5f
    Author: Ryan Neufeld <rneufeld@opendns.com>
    Date: Tue Jul 4 17:26:42 2017 -0700
    Updating README.md and Renaming files to meet standards
    [1x_LRS-350_12_bottom.stl, 1x_LRS-350_12_top.stl, 1x_LRS-350_enclosure_body.stl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]
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2017-07-10 Optional LCD mount providing clearance for pot
    - A modified version of the normal LCD mounts for the
    LCD to the extrusion.
    - This version provides additional clearance for the LCD’s
    contrast pot since it sticks out of the board on my 3rd
    party 2004 LCD Smart Controller Display
    [1x_lcd_mount_extra_contrast_clearence.stl]
2017-07-12 Add files via upload
    Added LCD mount clip version
    [1xlcd_mount_3030_clips.stl]
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2017-07-14 Add optional end-caps modified to fit T-Sun extrusion and update readme.
    [7x_tsun_end_cap.stl]
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2017-08-18 Added 3030 LCD clips with extra clearance
    [1x_lcd_mount_3030_extra_contrast_clearence.stl.stl]
2017-09-26 Added 2mm extra clearance in optional y-rod holders. (#54)
    Myself and a few others have needed some extra clearance for variations
    in the cut length of the y-rods. This part gives an extra 4mm total
    clearance, if used on both ends, without giving up too much strength.
    [4x_y_rod_holder_2mm_extra_clearance.stl]
2017-10-04 Extended the base of the enclosure to not require support. (#57)
    [1x_LRS-350_enclosure_body.stl]
2017-10-09 Updated the e-motor holder to decreas the angle on the PTFE tube.
    [1x_e_motor_holder.stl]
2017-10-16 LED Strip/Bar Holders for Haribo
    A collection of 3 variations of LED Holder designed for the Haribo.
    [LED_Holder_Haribo_v3.stl, LED_Holder_Haribo_v3_Bracket_Mount.stl, LED_Holder_Haribo_v3_Reversed_Mount.stl]
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2017-11-18 Removing duplicated belt holder. Adding two more options.
    [1x_modified_stock_y_belt_holder.stl, MK2S-modified-y-belt-holder-3mm-taller.stl, MK2S-modified-y-belt-holder.stl]
2017-12-04 Moving fixed files up to main directory. They're fine for general use
    [1x_power_supply_mounts-fix.stl, 1x_power_supply_mounts.stl, 1x_rambo_mount-fix.stl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]
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2018-01-18 Fixing nut slots
    [1x_LRS-350_enclosure_body.stl]
2018-01-18 Fixing it....again
    [1x_LRS-350_enclosure_body.stl]
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2018-01-18 Fixing orientation to be printable on open
    [1x_LRS-350_enclosure_body.stl]
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2018-02-06 reworked the slots
    [1x_lcd_mount_extended_pcb_ears_part1_SSE.stl, 1x_lcd_mount_extended_pcb_ears_part2_SSE.stl, 1x_power_supply_mount_center_SSE.stl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]
2018-05-19 Add files via upload
    Larger spaced T and L brackets as modeled by davvyk
    [2x_T_bracket_16mm_spacing.stl, 6x_L_bracket_16mm_spacing.stl]
2018-05-20 Added 16mm spacing for tnuts in affected parts
    Grouped files in a folder
    [1x_y_idler_16mm.stl, 1x_y_motor_mount_16mm.stl, 1x_z_motor_mounts_16mm.stl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]
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2018-05-25 Added new spool holder that resembles the MK3 B4 holder
    [Spool-holder-slide-top.stl]
2018-07-19 Removed front inner screw holes to prevent collisions
    [1x_z_motor_mounts_three_screw.stl]
2018-08-07 Updating y-belt holder to be based on teh MK2S, extended by 2mm
    [1x_y_belt_holder.stl]
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
